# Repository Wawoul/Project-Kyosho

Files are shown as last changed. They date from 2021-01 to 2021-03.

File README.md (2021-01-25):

# Project-Kyosho
Installing an array of sensors and leds into a RC nitro truggy

------------------------------------------------------------

The truggy: Kyosho Inferno ST  
Controller: 6 Channel FS-GT5 cw FS-BS6

Electronic mods;  
Toggable LED headlights & backlights  
Channel controlled RGB LED underlights  
Throttle servo failsafe module  
Channel controlled engine kill switch  
Fuel tank level sensor  
Engine block temperature sensor  
LCD Display screen  

Electronics used;  
FlySky FS-GT5 2.4G 6CH AFHDS RC Transmitter With FS-BS6 Receiver  
Longruner with ArduinoIDE ATmega328P Micro Controller  
AZDelivery HD44780 16x2 Serial LCD  
One Channel Relay Modules (x2)  
RC Dr. Mad Thrust Electronic Receiver Operated On/Off Switch (x2)  
4pcs RC Model Drift Car LED  
EBOWA Electric Air Water Valve DC 6V  
HUABAN DS18B20 Temperature Sensor Module  
Poweradd EnergyCell 5000mAh Portable Charger  
DFROBOT Non-contact Liquid Level Switch
LED strip - TBC

~ Images/Videos - https://photos.app.goo.gl/QmSYSMhcgNzhQ3Vj7 ~

Project contains (questionable drawn) circuit diagram + Test Sketches

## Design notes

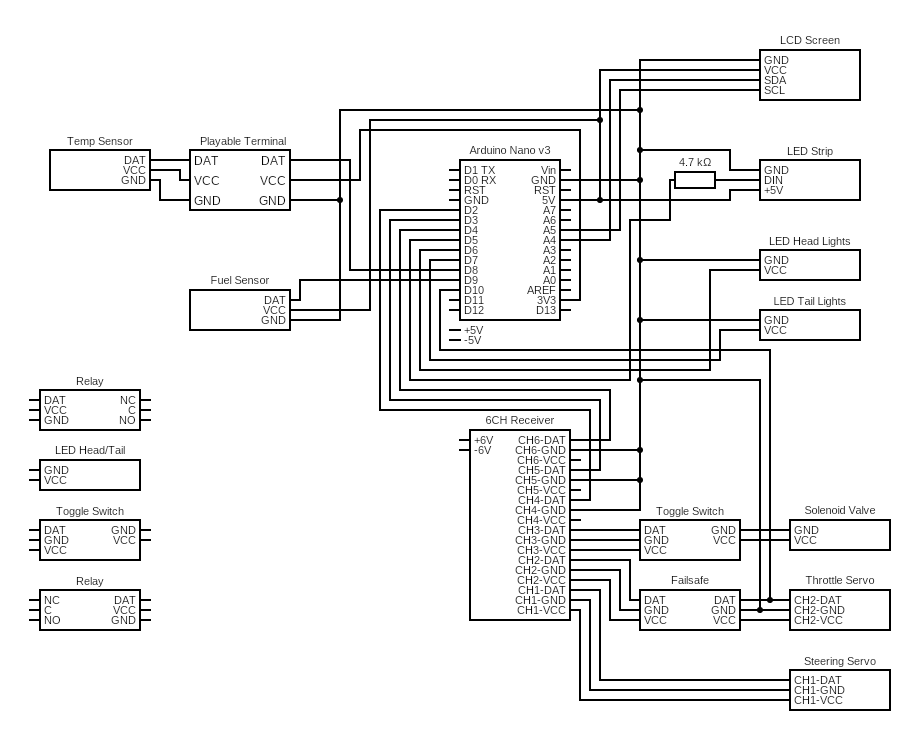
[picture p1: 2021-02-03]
Diagrams/circuitV3.png

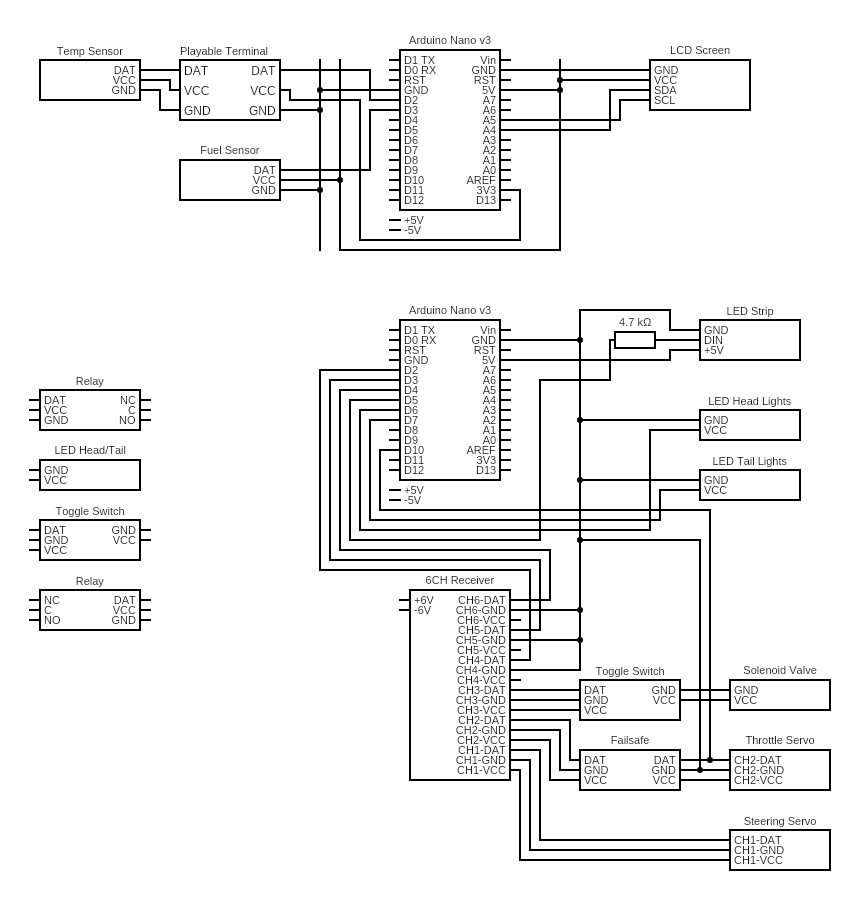
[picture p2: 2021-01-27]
Diagrams/circuitV2.png

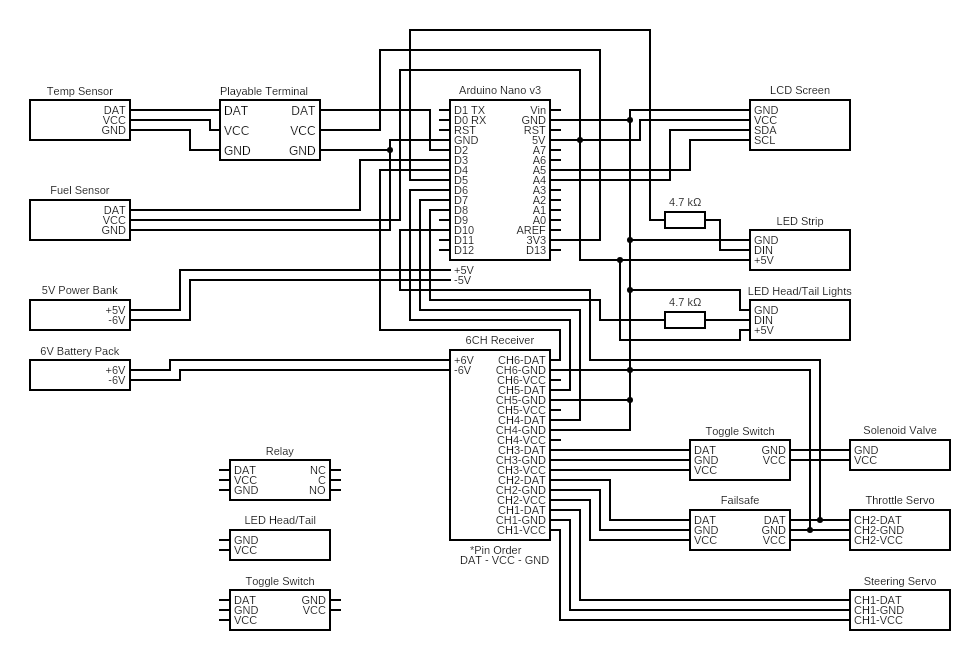
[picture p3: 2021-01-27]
Diagrams/circuitV1.png

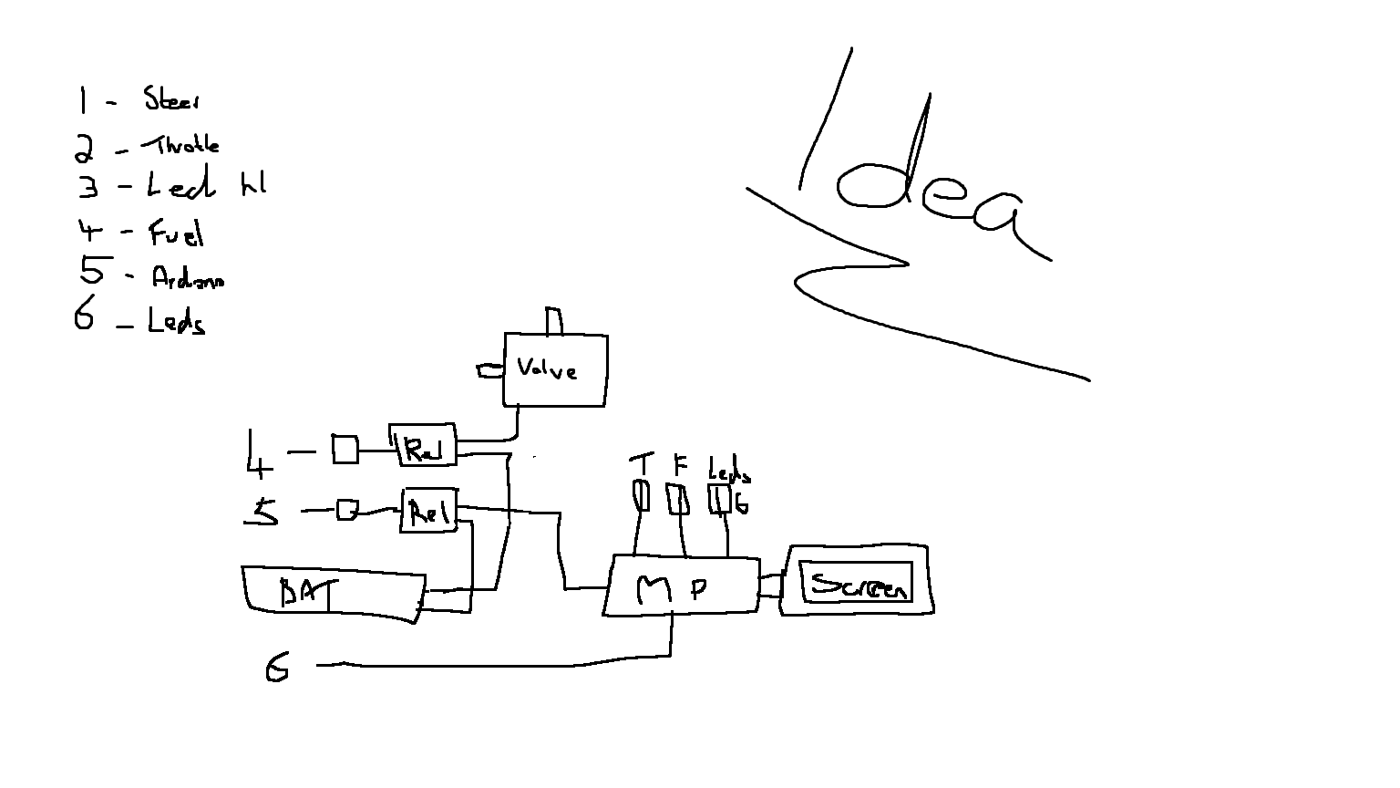
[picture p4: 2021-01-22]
Diagrams/The idea.png

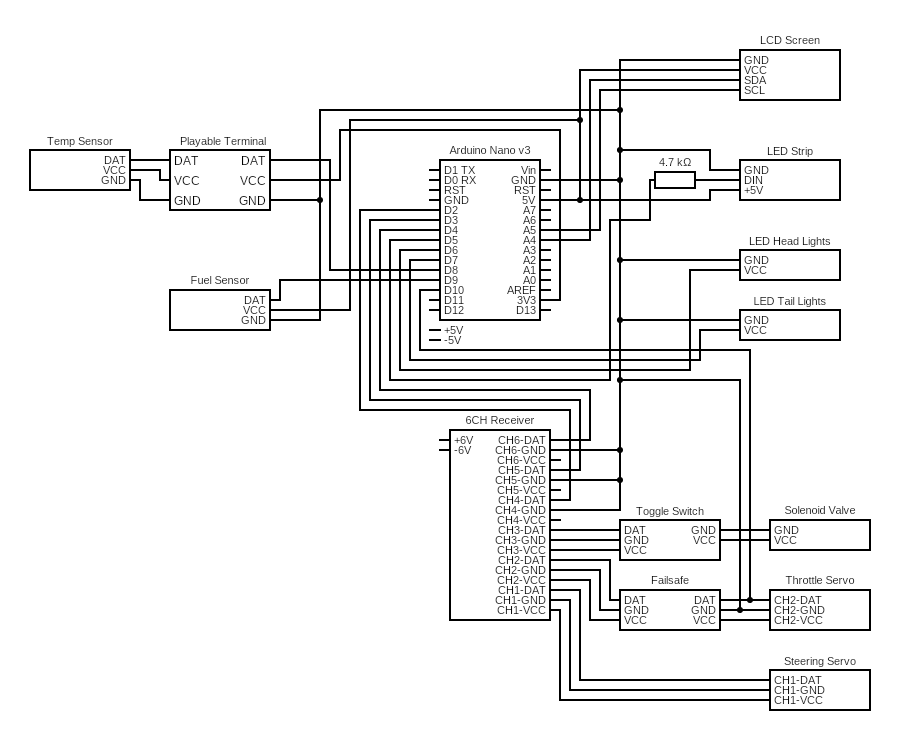
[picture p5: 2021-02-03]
Diagrams/circuitV3.1.png

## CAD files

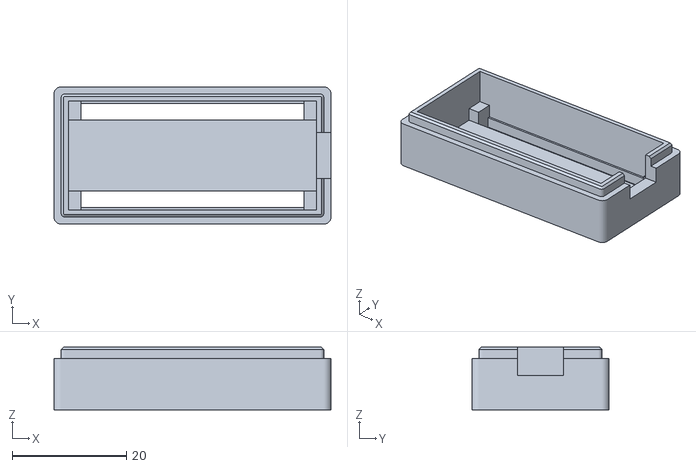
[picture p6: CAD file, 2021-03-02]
3D Prints/Arduino Case/NANOCASE-bottom.stl
48.5 x 24.0 x 11.0

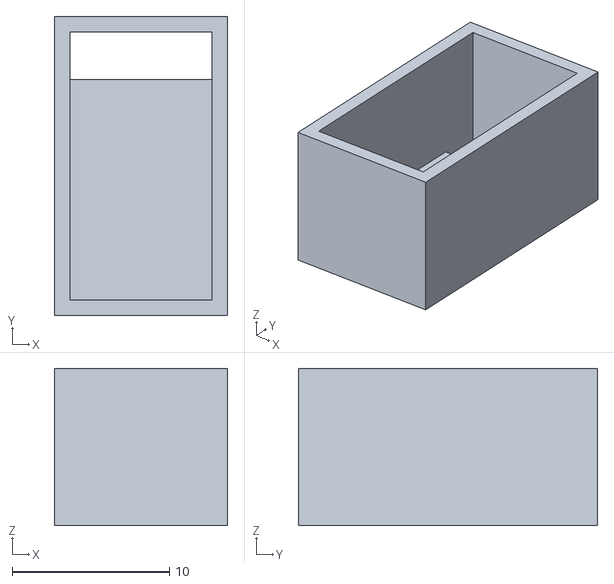
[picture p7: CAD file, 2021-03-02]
3D Prints/Fuel Sensor Cover/fuel box.stl
11.0 x 19.0 x 10.0

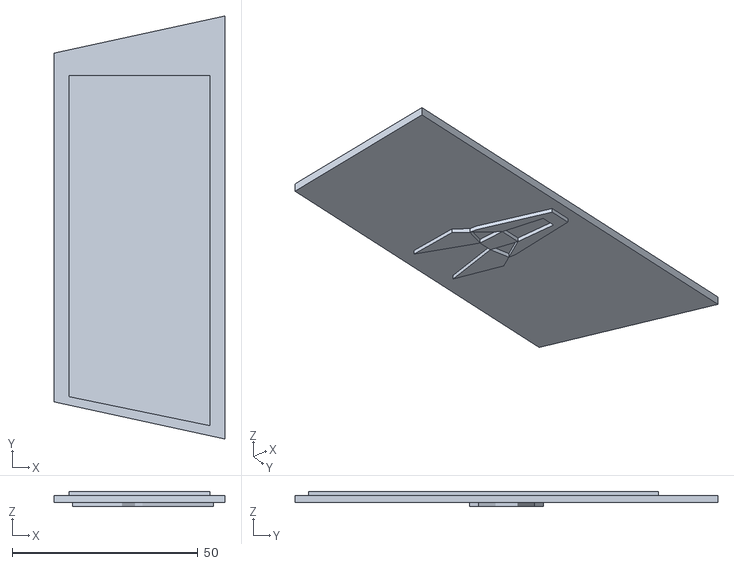
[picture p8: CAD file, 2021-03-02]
3D Prints/LCD Case/LCD lid.stl
46.0 x 114.0 x 4.00

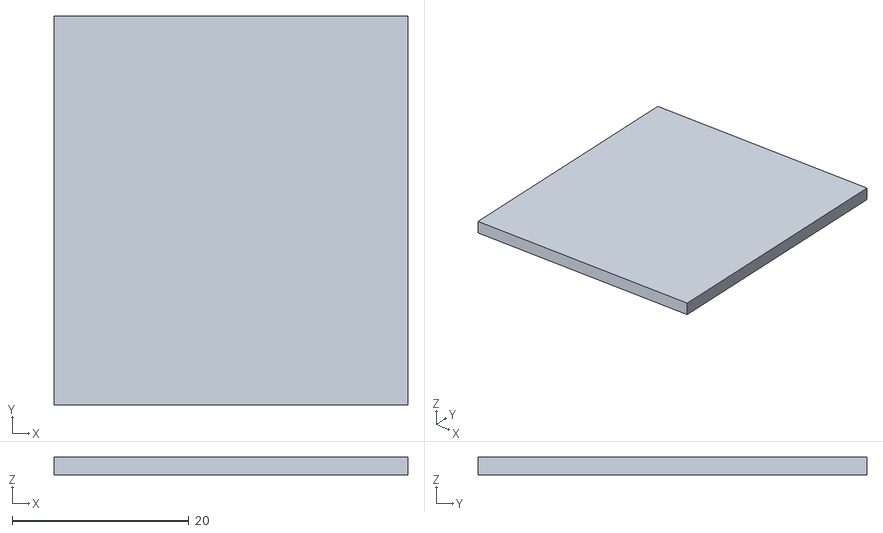
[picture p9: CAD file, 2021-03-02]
3D Prints/Light connecter Case/lights lid.stl
40.0 x 44.0 x 2.00

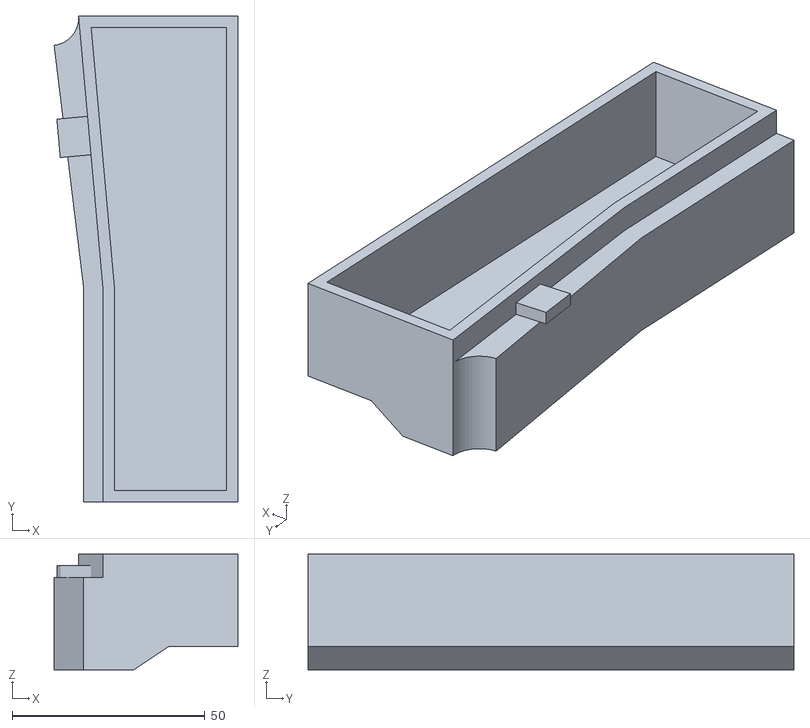
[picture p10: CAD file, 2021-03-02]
3D Prints/Power Bank Case/pb base.stl
47.7 x 126.0 x 30.0

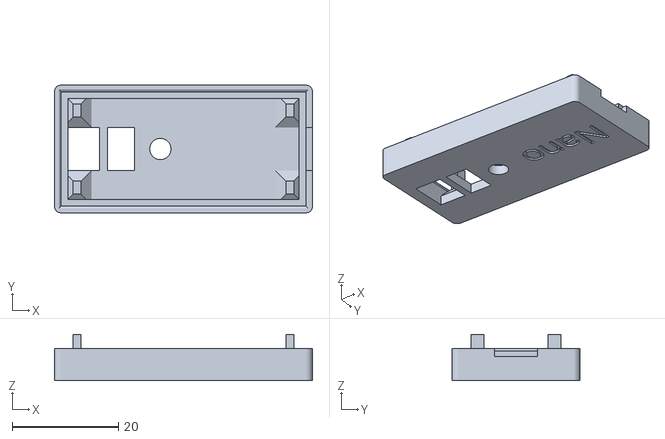
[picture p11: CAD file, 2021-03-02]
3D Prints/Arduino Case/NANOCASE-top-0.stl
48.5 x 24.0 x 8.70

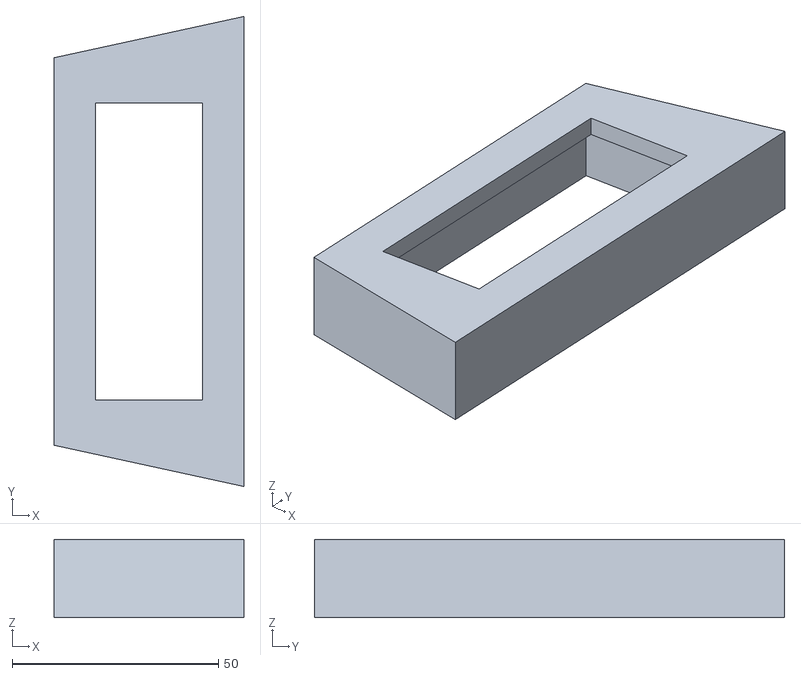
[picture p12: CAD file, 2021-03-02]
3D Prints/LCD Case/LCD Base.stl
46.0 x 114.0 x 19.0

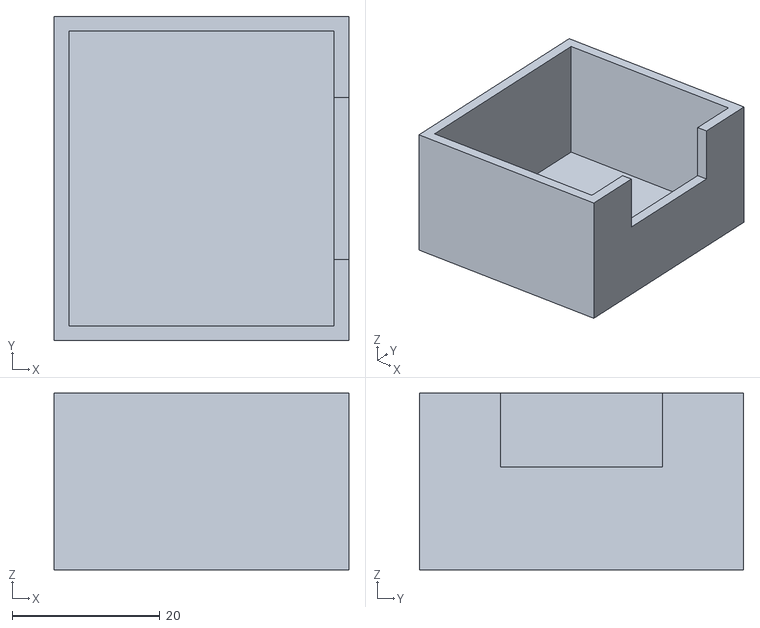
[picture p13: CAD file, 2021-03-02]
3D Prints/Light connecter Case/lights case.stl
40.0 x 44.0 x 24.0

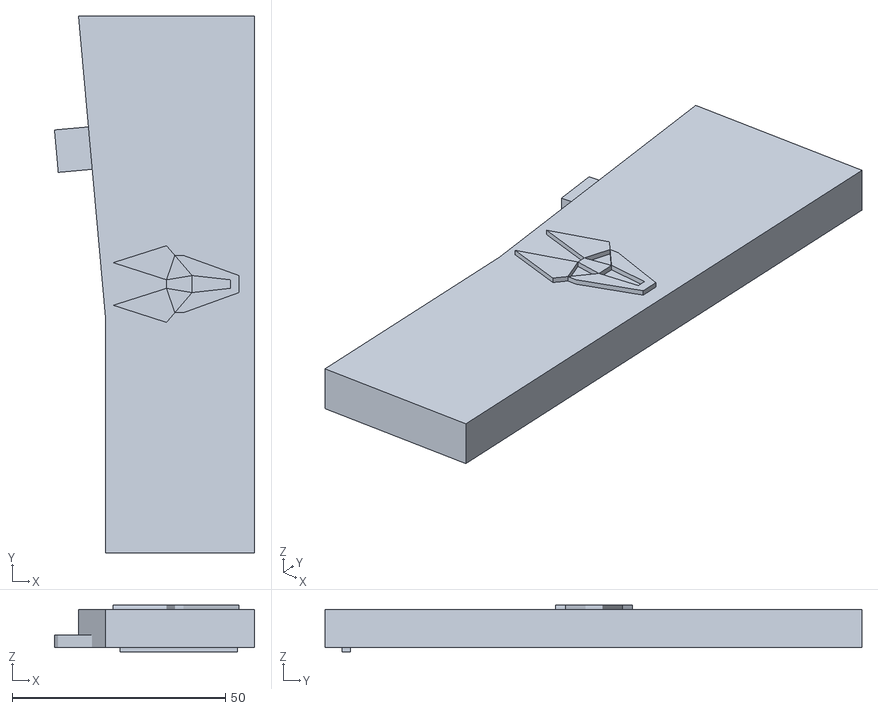
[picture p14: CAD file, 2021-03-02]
3D Prints/Power Bank Case/pb lid.stl
47.0 x 126.0 x 11.0

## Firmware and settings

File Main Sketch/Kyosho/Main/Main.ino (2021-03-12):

//--------------------------------------------------------------------------------------
//  Project Kyosho - 12/03/2021
//  By Ewen Paterson - Rev 5.1
//
//  Code for fuel and temp sensor fitted to a RC nitro truggy
//  Including RGB Leds and led head/tail lights
//
//  ArduinoIDE ATmega328P Micro Controller
//--------------------------------------------------------------------------------------

#include <Wire.h>
#include <LiquidCrystal_I2C.h>
#include <OneWire.h>  // Including the library of DS1820 Temperature module
#include <DallasTemperature.h>  // Including the library of DS1820 Temperature module
#include <Adafruit_NeoPixel.h>
#define ONE_WIRE_BUS 8             // Initializing the Arduino pin 8 for temperature module

OneWire ourWire(ONE_WIRE_BUS);     // Declaring a variable named our wire
DallasTemperature sensors ( &ourWire ); // Asking the Dallas temperature library to use the one wire library
LiquidCrystal_I2C lcd = LiquidCrystal_I2C(0x27, 16, 2); // LCD Setup
int tempPin = 8; //Temp Sen
int introFlag = 0;

#define N_LEDS 46  // Num of Under LEDS

int ledHead = 6; // Head light LEDs
int ledTail = 7; // Tail light LEDs

byte PWM_PIN1 = 3; // Pin D3 onnected to CH5 of receiver
byte PWM_PIN2 = 10; // Pin D10 Connected to CH2 of receiver
byte PWM_PIN3 = 2; // Pin D2 Connected to CH4 of receiver
byte PWM_PIN4 = 4; // Pin D4 Connected to CH6 of receiver

int pwm_value1;
int pwm_value2;
int pwm_value3;
int pwm_value4;

const int ledPin5 = 5; // LED Strip
const int ledPin7 = 7; // Head light LEDs
const int ledPin6 = 6; // Tail light LEDs
Adafruit_NeoPixel strip = Adafruit_NeoPixel(N_LEDS, ledPin5, NEO_GRB + NEO_KHZ800); // Under LEDs

//-----------------------------------
// SETUP
//-----------------------------------

void setup() {
 lcd.init();    //LCD Screen
 lcd.backlight(); //LCD Screen
 sensors.begin(); //Temp Sensor
 pinMode(9, INPUT); //Fuel Sensor

 strip.begin(); //Under LED Start
  strip.show(); //Initialize all pixels to 'off'
  strip.setBrightness(10); //Sets LEDs brightness

  pinMode(PWM_PIN1, INPUT);
  pinMode(PWM_PIN2, INPUT);
  pinMode(PWM_PIN3, INPUT);
  pinMode(PWM_PIN4, INPUT);

  pinMode(ledPin5, OUTPUT); // LED Strip
  pinMode(ledPin6, OUTPUT); // Tail light LEDs
  pinMode(ledPin7, OUTPUT); // Head light LEDs

  Serial.begin(115200);
}

//-----------------------------------
// LOOP
//-----------------------------------

void loop() {
 //Start-up Display
 if (introFlag == 0){ 
   lcd.clear();
   lcd.setCursor(0, 0);      // start to print at the first row
   lcd.print("   - KYOSHO -");
   lcd.setCursor(0, 1);
   lcd.print("* THE KAMIKAZE *");
   delay(3000);  
   lcd.clear();
   introFlag = 1;
 }

//-----------------------------------
// //Fuel Display                                    
 lcd.setCursor(0, 0);
 if (digitalRead(9) == HIGH) {
  lcd.print("Fuel  : LOW");
 } else {
  lcd.print("Fuel  : OK ");
 }

////-----------------------------------
// //Temp Display    
 sensors.requestTemperatures();
 lcd.setCursor(0, 1);      // start to print at the first row
 lcd.print("Engine: ");
 lcd.print(sensors.getTempCByIndex(0)-7, 1);    // print the temperature in Celsius
 lcd.print((char)223);      // print ° character
 lcd.print("C");
 //delay(500);


  pwm_value1 = pulseIn(PWM_PIN1, HIGH); // Pin D3 onnected to CH5 of receiver
  pwm_value2 = pulseIn(PWM_PIN2, HIGH); // Pin D10 Connected to CH2 of receiver
  pwm_value3 = pulseIn(PWM_PIN3, HIGH); // Pin D2 Connected to CH4 of receiver
  pwm_value4 = pulseIn(PWM_PIN4, HIGH); // Pin D4 Connected to CH6 of receiver

  // CH5 signal
  if (pwm_value1 < 1050 && pwm_value4 < 1050) {
    digitalWrite(ledPin5, LOW);
    Serial.println(pwm_value1);
                      for (int i = 0; i < N_LEDS; ++i)
                      {
                        strip.setPixelColor(i, 0, 0, 0); 
                      }
                      strip.show();
                    }
                  
  else if (pwm_value1 > 1101 && pwm_value1 < 1200) {
    digitalWrite(ledPin5, LOW);
    Serial.println(pwm_value1);
                      for (int i = 0; i < N_LEDS; ++i)
                      {
                        strip.setPixelColor(i, 0, 0, 255); //Blue
                      }
                      strip.show();
                    }
  else if (pwm_value1 > 1201 && pwm_value1 < 1400) {
      digitalWrite(ledPin5, LOW);
       for (int i = 0; i < N_LEDS; ++i)
                        {
                          strip.setPixelColor(i, 100, 100, 0); //Yellow
                        }
                        strip.show();
                      }
  else if (pwm_value1 > 1401 && pwm_value1 < 1600) {
      digitalWrite(ledPin5, LOW);
       for (int i = 0; i < N_LEDS; ++i)
                        {
                          strip.setPixelColor(i, 255, 0, 0); //Red
                        }
                        strip.show();
                      }
  else if (pwm_value1 > 1601 && pwm_value1 < 1800) {
      digitalWrite(ledPin5, LOW);
       for (int i = 0; i < N_LEDS; ++i)
                        {
                          strip.setPixelColor(i, 0, 255, 0); //Green
                        }
                        strip.show();
                      }
  else if (pwm_value1 > 1801 && pwm_value1 < 1995) {
      digitalWrite(ledPin5, LOW);
       for (int i = 0; i < N_LEDS; ++i)
                        {
                          strip.setPixelColor(i, 255, 255, 255); //White
                        }
                        strip.show();
   }

  // CH6 signal
  if (pwm_value4 < 1100 && pwm_value1 < 1100) {
    digitalWrite(ledPin5, LOW);
    Serial.println(pwm_value1);
                      for (int i = 0; i < N_LEDS; ++i)
                      {
                        strip.setPixelColor(i, 0, 0, 0); 
                      }
                      strip.show();
                    }
  else if (pwm_value4 > 1200 && pwm_value4 < 1500) {
      digitalWrite(ledPin5, LOW);
      PoliceLights(50);   // Police effect
                        }
  else if (pwm_value4 > 1501 && pwm_value4 < 1750) {
      digitalWrite(ledPin5, LOW);
      CylonBounce(0, 0, 0xff, 4, 10, 50);   //Cylon effect
                        }
  else if (pwm_value4 > 1751 && pwm_value4 < 1995) {
      digitalWrite(ledPin5, LOW);
      rainbowCycle(20);   //Rainbow effect
   }

  // Break Light signal                  
  if (pwm_value2 >= 1500) {
    digitalWrite(ledPin7, HIGH);  // turn brake light on
    Serial.println(pwm_value2);
  }
  else {
    digitalWrite(ledPin7, LOW);
  }

  // CH4 signal 
  if (pwm_value3 > 1470 && pwm_value3 < 1500) {  
    digitalWrite(ledPin6, HIGH);
    Serial.println(pwm_value3);
  }
  else if (pwm_value3 > 1500) {
    digitalWrite(ledPin6, HIGH);
    digitalWrite(ledPin7, HIGH);
    delay(500);
    digitalWrite(ledPin6, LOW);
    digitalWrite(ledPin7, LOW);
    Serial.println(pwm_value3);
  }
  else {
    digitalWrite(ledPin6, LOW);
  }
}

/////////////////////////////
// Effect Classes

// Rainbow effect
void rainbowCycle(int SpeedDelay) {
  byte *c;
  uint16_t i, j;

  for(j=0; j<256*5; j++) { // 5 cycles of all colors on wheel
    for(i=0; i< N_LEDS; i++) {
      c=Wheel(((i * 256 / N_LEDS) + j) & 255);
      strip.setPixelColor(i, *c, *(c+1), *(c+2));
    }
    strip.show();
    delay(SpeedDelay);
  }
}

byte * Wheel(byte WheelPos) {
  static byte c[3];
 
  if(WheelPos < 85) {
   c[0]=WheelPos * 3;
   c[1]=255 - WheelPos * 3;
   c[2]=0;
  } else if(WheelPos < 170) {
   WheelPos -= 85;
   c[0]=255 - WheelPos * 3;
   c[1]=0;
   c[2]=WheelPos * 3;
  } else {
   WheelPos -= 170;
   c[0]=0;
   c[1]=WheelPos * 3;
   c[2]=255 - WheelPos * 3;
  }

  return c;
}

// Fade In and Fade Out effect
void setAll(byte red, byte green, byte blue) {
  for(int i = 0; i < N_LEDS; i++ ) {
    strip.setPixelColor(i, red, green, blue);
  }
  strip.show();
}

void RGBLoop(){
  for(int j = 0; j < 3; j++ ) {
    // Fade IN
    for(int k = 0; k < 256; k++) {
      switch(j) {
        case 0: setAll(k,0,0); break;
        case 1: setAll(0,k,0); break;
        case 2: setAll(0,0,k); break;
      }
      strip.show();
      delay(3);
    }
    // Fade OUT
    for(int k = 255; k >= 0; k--) {
      switch(j) {
        case 0: setAll(k,0,0); break;
        case 1: setAll(0,k,0); break;
        case 2: setAll(0,0,k); break;
      }
      strip.show();
      delay(3);
    }
  }
}

// Cylon effect
void CylonBounce(byte red, byte green, byte blue, int EyeSize, int SpeedDelay, int ReturnDelay){

  for(int i = 0; i < N_LEDS-EyeSize-2; i++) {
    setAll(0,0,0);
    strip.setPixelColor(i, red/10, green/10, blue/10);
    for(int j = 1; j <= EyeSize; j++) {
      strip.setPixelColor(i+j, red, green, blue);
    }
    strip.setPixelColor(i+EyeSize+1, red/10, green/10, blue/10);
    strip.show();
    delay(SpeedDelay);
  }

  delay(ReturnDelay);

  for(int i = N_LEDS-EyeSize-2; i > 0; i--) {
    setAll(0,0,0);
    strip.setPixelColor(i, red/10, green/10, blue/10);
    for(int j = 1; j <= EyeSize; j++) {
      strip.setPixelColor(i+j, red, green, blue);
    }
    strip.setPixelColor(i+EyeSize+1, red/10, green/10, blue/10);
    strip.show();
    delay(SpeedDelay);
  }
 
  delay(ReturnDelay);
}

// PoliceLights
void PoliceLights(int fDelay){
for (int i = 0; i < 2; ++i) {
  for (int i = 0; i < N_LEDS/2; ++i)
                      {
                        strip.setPixelColor(i, 37, 0, 224); 
                      }
                      strip.show();
                      delay(fDelay);
  for (int i = 0; i < N_LEDS; ++i)
                      {
                        strip.setPixelColor(i, 0, 0, 0); 
                      }
                      strip.show();
                      delay(fDelay);
  for (int i = 0; i < N_LEDS/2; ++i)
                      {
                        strip.setPixelColor(i, 37, 0, 224); 
                      }
                      strip.show();
                      delay(fDelay);
  for (int i = 0; i < N_LEDS; ++i)
                      {
                        strip.setPixelColor(i, 0, 0, 0); 
                      }
                      strip.show();
                      delay(fDelay);
  for (int i = 0; i < N_LEDS; ++i)
                      {
                        strip.setPixelColor(i+23, 37, 0, 224); 
                      }
                      strip.show();
                      delay(fDelay);
  for (int i = 0; i < N_LEDS; ++i)
                      {
                        strip.setPixelColor(i, 0, 0, 0); 
                      }
                      strip.show();
                      delay(fDelay);
  for (int i = 0; i < N_LEDS/2; ++i)
                      {
                        strip.setPixelColor(i+23, 37, 0, 224); 
                      }
                      strip.show();
                      delay(fDelay);
  for (int i = 0; i < N_LEDS; ++i)
                      {
                        strip.setPixelColor(i, 0, 0, 0); 
                      }
                      strip.show();
  }
}

//////////////////////////////
// Channel Values:
// CH6 PWM Range - LED effects~
//Top - 995-1100 - OFF
//Mid - 1251-1500 - PoliceLights
//Mid - 1501-1750 - CylonBounce
//Bot - 1751-1995 - Rainbow
//
//CH5 PWM Range - LED Static colours~
//Top - 995-1100 - OFF
//Mid - 1101-1200 - Blue
//Mid - 1201-1400 - Yellow
//Mid - 1401-1600 - Red
//Mid - 1601-1800 - Green
//Bot - 1801-1995 - White
//
//CH4 PWM Range - Off>Head Lights/Hazards~
//Bot - 995-996
//Mid - 1490-1498
//Top - 1985-1991
//
//CH2 (Throttle)PWM Range~
//Idle - 1490-1496
//Break - 1496-1991
//Accelerate - 995-1490
//////////////////////////////

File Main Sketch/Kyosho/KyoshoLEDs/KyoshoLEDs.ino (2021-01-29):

//--------------------------------------------------------------------------------------
//  Project Kyosho - 29/01/2021
//  By Ewen Paterson - Rev 4
//
//  Code for leds in a RC nitro truggy
//
//  ArduinoIDE ATmega328P Micro Controller
//--------------------------------------------------------------------------------------
//////////////////////////////
// CH6 PWM Range - LED effects~
// Top - 995-996
// Mid - 1490-1498
// Bot - 1985-1991
// 1- 950-1080  -off
// 2- 1082-1210  - Blue
// 3- 1210-1340  - Red
// 4 - 1340-1470  - Yellow
// 5- 1470-1600  - White
// 6- 1600-1730  - Fade
// 7- 1730-1860  - Rainbow
// 8- 1860-1990  - Police
//
//CH5 PWM Range - LED Static colours~
//Top - 995-996
//Mid - 1450-1456
//Bot - 1988-1995
//
//CH4 PWM Range - Off>Head/Tail>LED Brightness~
//Bot - 995-996
//Mid - 1490-1498
//Top - 1985-1991
//
//CH2 (Throttle)PWM Range~
//Idle - 1490-1496
//Break - 1496-1991
//Accelerate - 995-1490
//////////////////////////////

#include <Adafruit_NeoPixel.h>
#define N_LEDS 44  // Num of Under LEDS

int ledHead = 6; // Head light LEDs
int ledTail = 7; // Tail light LEDs

byte PWM_PIN1 = 3; // Pin D3 onnected to CH5 of receiver
byte PWM_PIN2 = 10; // Pin D10 Connected to CH2 of receiver
byte PWM_PIN3 = 2; // Pin D2 Connected to CH4 of receiver
byte PWM_PIN4 = 4; // Pin D4 Connected to CH6 of receiver

int pwm_value1;
int pwm_value2;
int pwm_value3;
int pwm_value4;

const int ledPin5 = 5; // LED Strip
const int ledPin7 = 7; // Head light LEDs
const int ledPin6 = 6; // Tail light LEDs

// Parameter 1 = number of pixels in strip
// Parameter 2 = Arduino pin number (most are valid)
// Parameter 3 = pixel type flags, add together as needed:
//   NEO_KHZ800  800 KHz bitstream (most NeoPixel products w/WS2812 LEDs)
//   NEO_KHZ400  400 KHz (classic 'v1' (not v2) FLORA pixels, WS2811 drivers)
//   NEO_GRB     Pixels are wired for GRB bitstream (most NeoPixel products)
//   NEO_RGB     Pixels are wired for RGB bitstream (v1 FLORA pixels, not v2)
//   NEO_RGBW    Pixels are wired for RGBW bitstream (NeoPixel RGBW products)
Adafruit_NeoPixel strip = Adafruit_NeoPixel(N_LEDS, ledPin5, NEO_GRB + NEO_KHZ800); // Under LEDs

//-----------------------------------
// Police LED Effect
//-----------------------------------
const int frameMax = 19;
int frames[frameMax][8][3] = {
  {{0, 0, 255 }, {0, 0, 255 }, {0, 0, 0 }, {0, 0, 0 }, {0, 0, 0 }, {0, 0, 0 }, {255, 0, 0 }, {255, 0, 0 }},
  {{0, 0, 0 }, {0, 0, 0 }, {0, 0, 0 }, {0, 0, 0 }, {0, 0, 0 }, {0, 0, 0 }, {255, 0, 0 }, {255, 0, 0 }},
  {{0, 0, 0 }, {0, 0, 0 }, {0, 0, 0 }, {0, 0, 0 }, {0, 0, 0 }, {0, 0, 0 }, {0, 0, 0 }, {0, 0, 0 }},
  {{0, 0, 255 }, {0, 0, 255 }, {0, 0, 0 }, {0, 0, 0 }, {0, 0, 0 }, {0, 0, 0 }, {0, 0, 0 }, {0, 0, 0 }},
  {{0, 0, 0 }, {0, 0, 0 }, {0, 0, 0 }, {0, 0, 0 }, {0, 0, 0 }, {0, 0, 0 }, {255, 0, 0 }, {255, 0, 0 }},
  {{0, 0, 0 }, {0, 0, 0 }, {0, 0, 0 }, {0, 0, 0 }, {0, 0, 0 }, {0, 0, 0 }, {0, 0, 0 }, {0, 0, 0 }},
  {{0, 0, 255 }, {0, 0, 255 }, {0, 0, 0 }, {0, 0, 0 }, {0, 0, 0 }, {0, 0, 0 }, {0, 0, 0 }, {0, 0, 0 }},
  {{0, 0, 0 }, {0, 0, 0 }, {0, 0, 0 }, {0, 0, 0 }, {0, 0, 0 }, {0, 0, 0 }, {255, 0, 0 }, {255, 0, 0 }},
  {{0, 0, 0 }, {0, 0, 0 }, {0, 0, 0 }, {255, 255, 255}, {255, 255, 255}, {0, 0, 0 }, {0, 0, 0 }, {0, 0, 0 }},
  {{0, 0, 0 }, {0, 0, 0 }, {0, 0, 0 }, {0, 0, 0 }, {0, 0, 0 }, {0, 0, 0 }, {0, 0, 0 }, {0, 0, 0 }},
  {{0, 0, 0 }, {0, 0, 0 }, {0, 0, 0 }, {255, 255, 255}, {255, 255, 255}, {0, 0, 0 }, {0, 0, 0 }, {0, 0, 0 }},
  {{0, 0, 0 }, {0, 0, 0 }, {0, 0, 0 }, {0, 0, 0 }, {0, 0, 0 }, {0, 0, 0 }, {0, 0, 0 }, {0, 0, 0 }},
  {{0, 0, 0 }, {255, 0, 0 }, {255, 0, 0 }, {255, 0, 0 }, {255, 0, 0 }, {0, 0, 0 }, {0, 0, 0 }, {0, 0, 0 }},
  {{0, 0, 0 }, {255, 0, 0 }, {255, 0, 0}, {0, 0, 0 }, {255, 0, 0 }, {0, 0, 0 }, {255, 0, 0 }, {255, 0, 0 }},
  {{0, 0, 255 }, {0, 0, 0 }, {0, 0, 0 }, {0, 0, 0 }, {0, 0, 0 }, {0, 0, 0 }, {0, 0, 0 }, {255, 0, 0 }},
  {{255, 255, 255}, {255, 255, 255}, {255, 255, 255}, {255, 255, 255}, {255, 255, 255}, {255, 255, 255}, {255, 255, 255}, {255, 255, 255}},
  {{0, 0, 255 }, {0, 0, 255 }, {0, 0, 0 }, {0, 0, 0 }, {0, 0, 0 }, {0, 0, 0 }, {0, 0, 0 }, {0, 0, 0 }},
  {{0, 0, 0 }, {0, 0, 0 }, {255, 255, 255}, {255, 255, 255}, {255, 255, 255}, {255, 255, 255}, {0, 0, 0 }, {0, 0, 0 }},
  {{0, 0,  0}, {0, 0, 0 }, {255, 0, 0}, {255, 0, 0 }, {255, 0, 0 }, {255, 0, 0 }, {0, 0, 0 }, {0, 0, 0 }}
};

int durations[frameMax] = {1000, 100, 100, 50, 50, 10, 50, 50, 50, 40, 50, 40, 100, 100, 100, 20, 40, 20, 100};
int frameCurrent = 0;

//-----------------------------------
// SETUP
//-----------------------------------

void setup() {
  strip.begin(); //Under LED Start
  strip.show(); //Initialize all pixels to 'off'
  strip.setBrightness(10); //Sets LEDs brightness

  pinMode(PWM_PIN1, INPUT);
  pinMode(PWM_PIN2, INPUT);
  pinMode(PWM_PIN3, INPUT);
  pinMode(PWM_PIN4, INPUT);

  pinMode(ledPin5, OUTPUT); // LED Strip
  pinMode(ledPin6, OUTPUT); // Tail light LEDs
  pinMode(ledPin7, OUTPUT); // Head light LEDs

  Serial.begin(115200);
}

//-----------------------------------
// LOOP
//-----------------------------------

void loop() {

  pwm_value1 = pulseIn(PWM_PIN1, HIGH); // Pin D3 onnected to CH5 of receiver
  pwm_value2 = pulseIn(PWM_PIN2, HIGH); // Pin D10 Connected to CH2 of receiver
  pwm_value3 = pulseIn(PWM_PIN3, HIGH); // Pin D2 Connected to CH4 of receiver
  pwm_value4 = pulseIn(PWM_PIN4, HIGH); // Pin D4 Connected to CH6 of receiver

  if (pwm_value1 > 1470) {
    digitalWrite(ledPin5, LOW);
    Serial.println(pwm_value1);
                      for (int i = 0; i < N_LEDS; ++i)
                      {
                        strip.setPixelColor(i, 0, 0, 0); 
                      }
                      strip.show();
                    }
                  
  else {
    digitalWrite(ledPin5, LOW);
     for (int i = 0; i < N_LEDS; ++i)
                      {
                        strip.setPixelColor(i, 255, 255, 255); //White
                      }
                      strip.show();
                    }
                    
  if (pwm_value2 >= 1500) {
    digitalWrite(ledPin7, HIGH);  // turn brake light on
    Serial.println(pwm_value2);
  }
  else {
    digitalWrite(ledPin7, LOW);
  }
  if (pwm_value3 > 1470) {
    digitalWrite(ledPin6, HIGH);
    Serial.println(pwm_value3);
  }
  else {
    digitalWrite(ledPin6, LOW);
  }
}
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

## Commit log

2021-01-25 Added wip circuit
2021-01-27 Rework
    Delay on LCD causing lag on LED change/tail lights. Split up the code for 2 arduinos
    [CH6_Test.ino, HeadTailLED_Test.ino, KyoshoLEDs.ino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]
2021-01-29 Rev 5
    Merging both main sketches and testing led latency
2021-02-03 updated circuit diagram
2021-03-02 Completed!
    Main code finished and tested
    [LCD Base.stl, LCD lid.stl, NANOCASE-bottom.stl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]
2021-03-12 Update Main.ino
    Calibrate temp
